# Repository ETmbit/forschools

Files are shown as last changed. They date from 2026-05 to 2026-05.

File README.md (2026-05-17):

ElecTricks


# Het ETmbit-project
Het ETmbit-project biedt een **complete leerlijn robotica** en maakt het lesgeven erin eenvoudig en toegankelijk. Het project is gericht op:
- bovenbouw basisonderwijs 
- onderbouw voortgezet onderwijs

ETmbit met **micro:bit + MakeCode**. Robotonderdelen worden **kant-en-klaar** aangeschaft of **3D-geprint**. Bij iedere module zit een **bouwgids** (inclusief bestellijsten en bestanden voor de 3D-printer), een **docentenhandleiding** en uiteraard het **lesmateriaal**. Van leerkrachten en docenten wordt **minimale voorkennis en voorbereiding** verwacht.

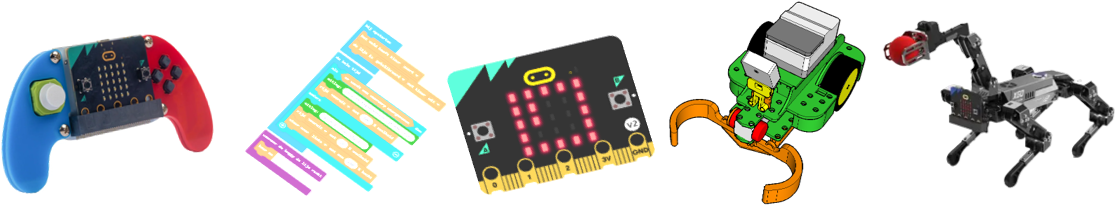
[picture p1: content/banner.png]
Banner


<br>

## :twisted_rightwards_arrows: Lesplan
ETmbit heeft **gedifferentieerd leren** als uitgangspunt. Leerlingen kiezen hun eigen route door het lesmateriaal op basis van interesse, niveau en leerstijl. Leerkrachten en docenten gebruiken een **volgsysteem** om hun ontwikkeling te begeleiden. Geen ingewikkelde sheets — alles werkt met voor zowel de leerlingen als de lesgevende **overzichtlijke routekaarten**.

:large_orange_diamond: [naar de routekaarten](NL/routekaarten/)

<br>

## :basket: Lesinhoud
Hier is **spelenderwijs leren** de boodschap. Het begint met enkele bekende spelletjes om te leren hoe MakeCode werkt: *kat-en-muis*, *snake*, *simon-says*. Het lesmateriaal biedt veel **challenges**. Via verschillende routes door het ETmbit-materiaal ontwikkelen leerlingen uiteindelijk dezelfde vaardigheden. Voor elk wat wils:

:soccer: sport, :musical_note: muziek, :cartwheeling: dans, :video_game: games, :seedling: natuur, :baby: verzorging, :nut_and_bolt: techniek, :clapper: beeld, enz.

:large_orange_diamond: [naar de lesmodules](NL/modules/)

<br><br>

## :movie_camera: En ...
Waarom *ElecTricks*? De naam komt van een tv-serie uit mijn jeugd:
<br><br>

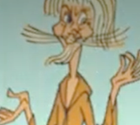
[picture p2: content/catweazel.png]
Catweazel


**Catweazel**. De in het heden belande middeleeuwse magiër, die de wonderlijke mogelijkheden van elektriciteit *Elec-Trickery* noemde.

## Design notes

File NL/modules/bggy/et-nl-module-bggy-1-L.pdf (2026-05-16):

45

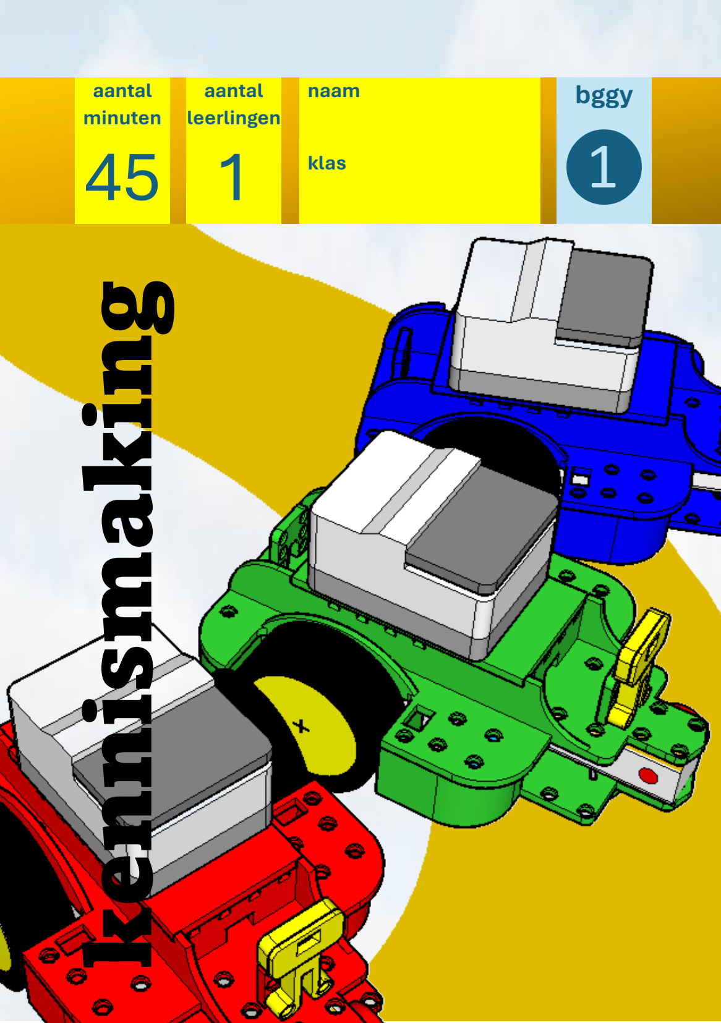
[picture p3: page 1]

bggy ❶

aantal
minuten

aantal
leerlingen 1

naam

klas

# kennismaking

### Nodig:

- De buggy
- Het veld voor de lijnvolger
- Een voorwerp van ongeveer 20 cm hoog en breed
- MakeCode
url = https://makecode.microbit.org
- Uitbreiding ETmbit/etbuggy
url = https://github.com/ETmbit/etbuggy

### Het blokkenmenu:

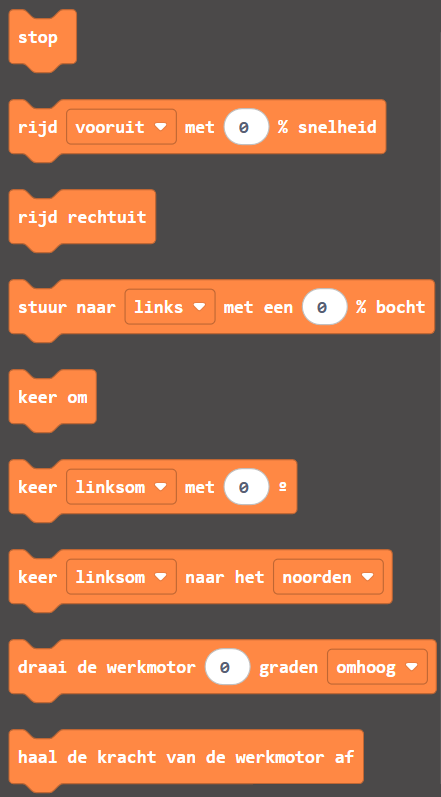
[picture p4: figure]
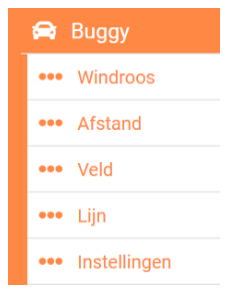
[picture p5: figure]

Voordat je begint moet je met de instellingen de buggy klaar maken om te programmeren.

In het hoofdmenu
hiernaast vind je de
blokken om de buggy
te besturen.
Met de blokken van de
extra menu’s hieronder,
gebruik je de sensoren.

### De buggy:

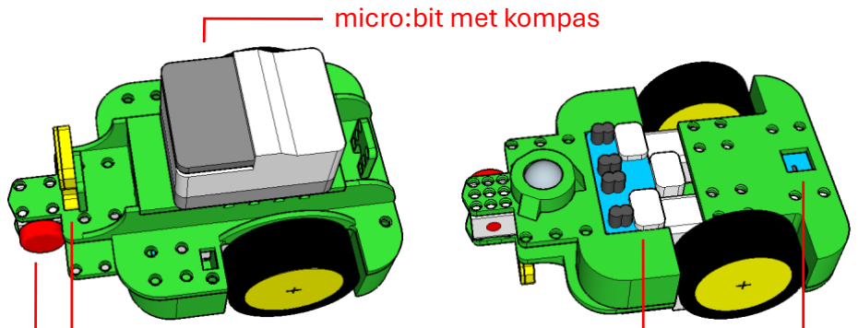
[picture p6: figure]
micro:bit met kompas

### Toelichting bij enkele codeblokken:

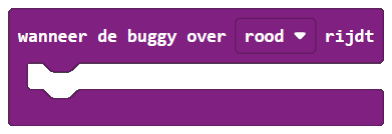
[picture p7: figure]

De kleur wordt door de veldsensor gemeten.
Een bocht van 0% gaat rechtuit. Bij een bocht van 100% draait de buggy om zijn as.
‘Omhoog’ betekent dat
de voorkant van de
motoras omhoog draait.
Normaal houdt de werkmotor iets opgetild.
werkmotor | afstandsensor | lijnsensor | veldsensor

### Begin met de instellingen:

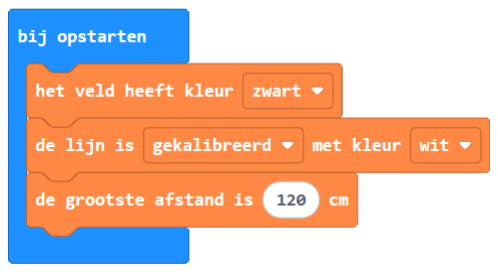
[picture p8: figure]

De belangrijkste instelling is die van de veldkleur. Als je die vergeet, zal de buggy niet rijden.
Het is het beste om de lijnsensor van de buggy op het veld met de lijn te kalibreren:

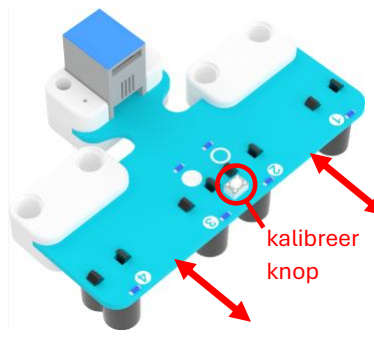
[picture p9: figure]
kalibreer knop

Je moet ook laten weten tot hoever de buggy afstanden zal meten. Daarbinnen mag niemand staan.

1. Druk op de kalibreerknop.
2. Leds 1 t/m 4 gaan om de beurt aan.
3. Leds ○ en ● knipperen snel.
4. De verlichting onder gaat aan.
5. Beweeg de sensor 1 cm boven de grond vanaf het veld over de lijn heen en weer.
6. Doe dit tot het knipperen stop.

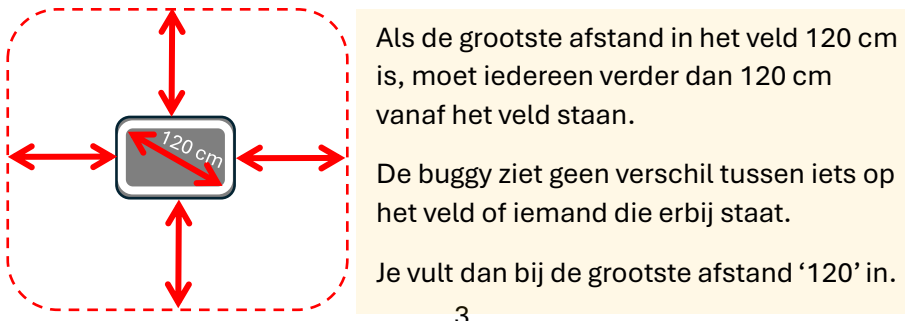
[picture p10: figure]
is, moet iedereen verder dan 120 cm vanaf het veld staan.; het veld of iemand die erbij staat.

Als de grootste afstand in het veld 120 cm

De buggy ziet geen verschil tussen iets op

Je vult dan bij de grootste afstand ‘120’ in.

### Probeer de volgende programma’s:

Gebruik nu het veld voor de lijnvolger. Dit heeft een witte lijn op een zwart veld.
Maak één voor één de volgende programma’s en kijk wat er wel/niet gebeurt. Begin steeds midden in het veld.
- 1

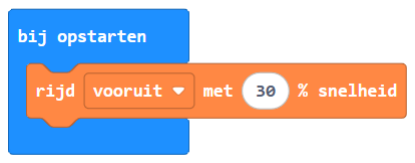
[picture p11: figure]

- 2

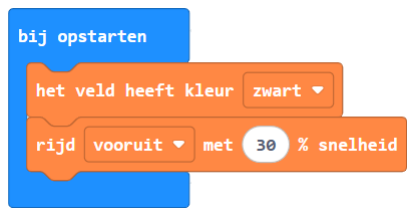
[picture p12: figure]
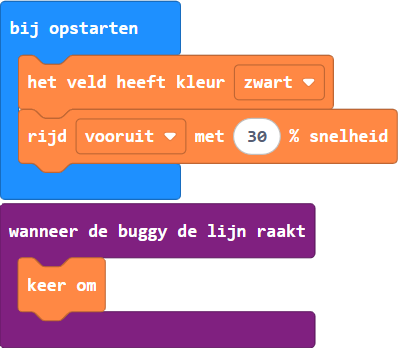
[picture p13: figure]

Let op: Vul de echte kleur van het veld in.

- 3

Laat de buggy naar een
voorwerp rijden.
- 4

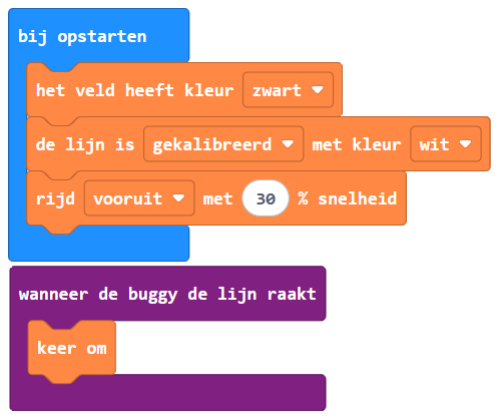
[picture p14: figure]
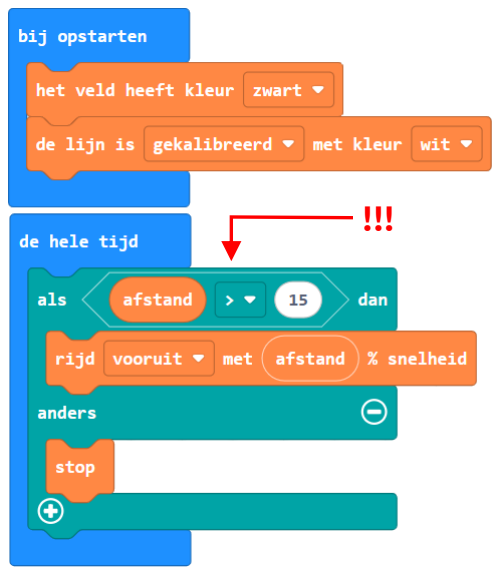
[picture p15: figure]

Let op: Vul de echte kleur van de lijn in.

- 5

### Verwerking:

Beantwoord de volgende vragen:
Wat gebeurt er als je geen veldkleur instelt?
- De buggy doet helemaal niets.
- De buggy begint, maar stopt meteen.
- De buggy doet het gewoon.
Waarom denk je dat dit zo is?
- Dan weet je dat de buggy iets doet.
- Anders kan de buggy van tafel rijden.
- Beiden zijn waar.
Hoe reageert de buggy op de lijn?
- Dat programmeer je met
- De buggy stopt op de lijn.
- De buggy keert om bij de lijn.
Wat moet je doen om | te laten werken?
- Het is genoeg om de buggy aan te zetten.
- Altijd als de buggy bij de lijn komt.
- Je moet niet vergeten de lijn in te stellen.
Bij programma 5 gaat de buggy steeds langzamer rijden. Welk blok doet dat?
○
○
○

### Zelf doen:

Denk om wat je tot nu toe hebt geleerd.
Je kunt ook de volgende blokken gebruiken:

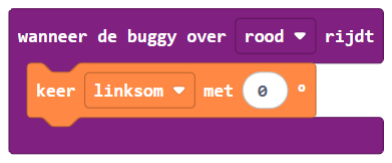
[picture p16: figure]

- 1

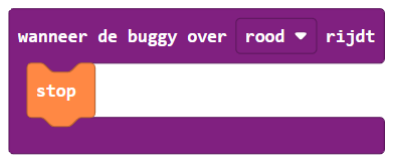
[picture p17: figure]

Maak een programma waarmee de buggy op een gekleurd vak stopt.

- 2
Maak een programma waarmee de buggy tussen de vier gekleurde vakken een rondje rijdt.

Tip.
Zo werkt het met graden:
0⁰ | 90⁰ | 180⁰ | 270⁰ | 360⁰

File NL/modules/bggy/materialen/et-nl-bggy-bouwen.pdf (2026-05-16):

# ETBUGGY

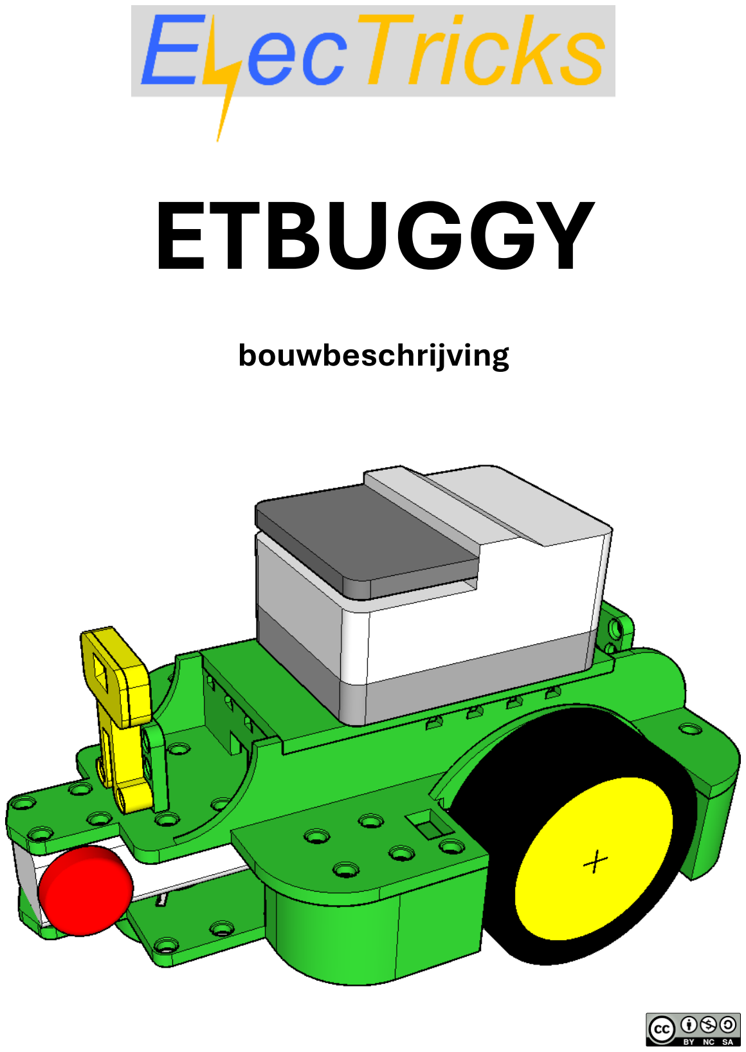
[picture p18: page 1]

bouwbeschrijving

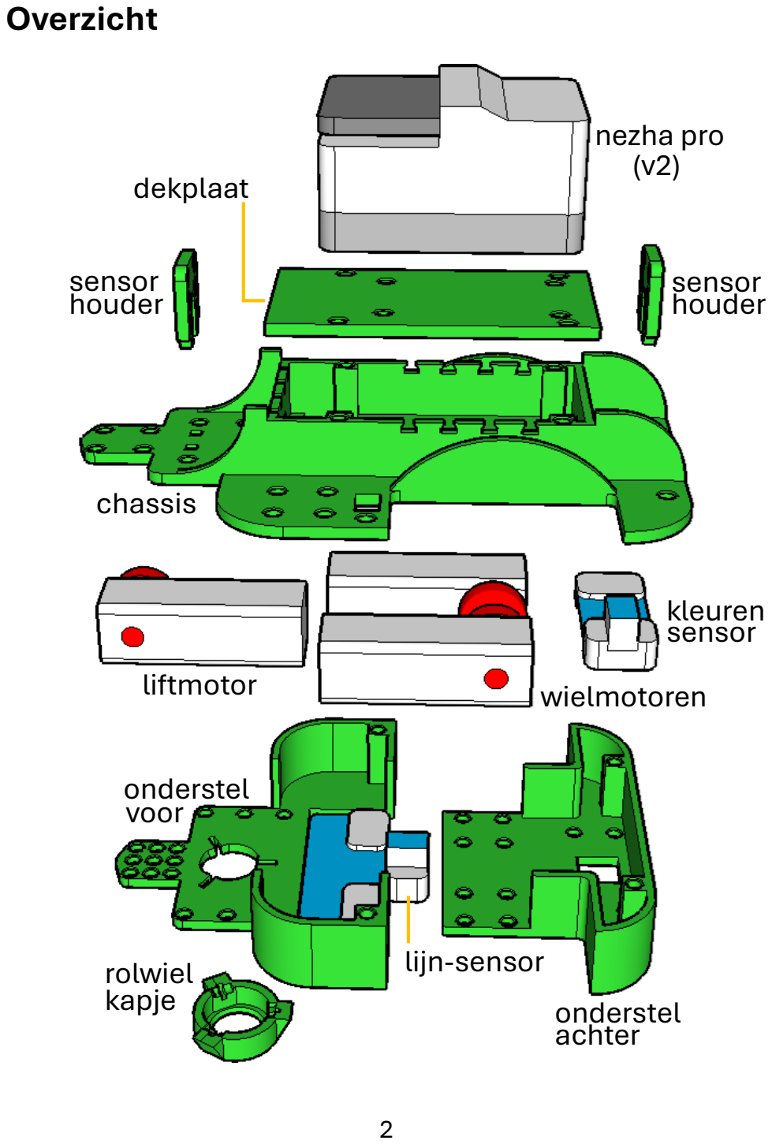
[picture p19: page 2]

Overzicht

chassis

dekplaat

nezha pro

sensor
houder

wielmotoren liftmotor

sensor
houder

onderstel
achter

onderstel
voor

lijn-sensor

(v2)

kleuren
sensor

rolwiel
kapje

Maken en kopen

De volgende onderdelen worden met een 3D-printer gemaakt. De stl-bestanden zijn te vinden in: https://github.com/etmbit/printables
chassis: | et-nl-bggy-chassis.stl
dekplaat: | et-nl-bggy-dekplaat.stl
onderstel voor: | et-nl-bggy-voorkant.stl
onderstel achter: | et-nl-bggy-achterkant.stl
sensorhouder voor: | et-nl-bggy-sensor-voor.stl
sensorhouder achter: et-nl-bggy-sensor-achter.stl
rolwielkapje: | et-nl-bggy-caster.stl
asje voor kogellager: et-nl-bggy-caster-asje.stl
lidar-afstandsensor: et-nl-bggy-lidar.stl | *)
wielasje TT/LEGO: | et-nl-bggy-tt2lego.stl
motoras met dop: | et-nl-bggy-motor-as.stl

*) Dit is de behuizing voor de VL53L1X-lidar (zie verderop).

De onderdelen voor het rolwiel (een kogel met drie lagers) zijn verkrijgbaar bij www.neita.nl/webshop:
Kogel: Home > Webshop > Lagers > Kogels
> Kogels 22mm DIN 5401 GD-20 Lagers: Home > Webshop > Lagers > Miniatuurlagers > PRC Miniatuur kogellager 1R (5x8x2,5)

De wielen en een lidar-afstandsensor zijn te bestellen bij www.tinytronics.nl/nl:
Wielen: | Home > Mechanica en Actuatoren > Onderdelen > Wielen > Reservewiel - Auto Kit - Zelfbouw

Afstandsensor: Home > Sensoren > Afstand
| > VL53L1X Time-of-Flight ToF
Voor de lidar-afstandsensor is het nodig om een aan één uiteinde gestripte PlanetX RJ11-kabel aan de VL53L1Xsensor te solderen. De behuizing kan met een 3D-printer worden gemaakt (gebruik het eerder genoemde bestand buggy-lidar.stl).
Aansluitschema:

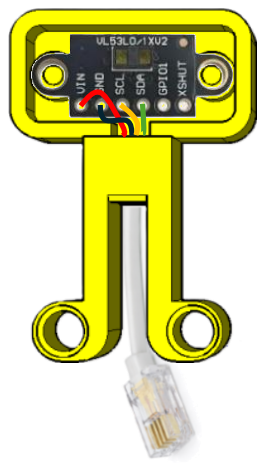
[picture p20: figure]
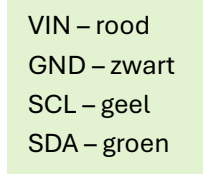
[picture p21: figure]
VIN – rood GND – zwart SCL – geel SDA – groen

In plaats van deze lidar, kan ook een ultrasone afstandsensor worden gebruik, zoals het kant-en-klare model uit de PlanetX-serie (zie hierna).

lijmen

De electronische onderdelen komen uit de PlanetX-serie van Elecfreaks en kunnen afzonderlijk worden besteld bij webshop.ictleskisten.nl/product-categorie/elecfreaks:
nezha pro: | Nezha PRO breakout board [EF05070]
motoren: | Smart Brick Motor [EF05071]
lijnsensor: | 4 Channel Tracking Sensor [EF05053]
kleurensensor: Colour Sensor [EF05006] afstandsensor: Ultrasonic Sensor [EF05007] *)
snoeren: | RJ11 4P4C 200 mm Kabel [EF05049]

*) Eventueel ter vervanging van de lidar-sensor (zie hiervoor).

Om de verschillende onderdelen aan elkaar te
bevestigen, zijn 36 pinnen | en 2 pinnen | nodig. Deze
zijn te verkrijgen bij www.steentjeswereld.nl:
pin | : | zoek LEGO-technic onderdeel 32002
pin | : | zoek LEGO-technic onderdeel 2780

De behuizing van de lidar-afstandsensor en het rolwielkapje moeten worden gelijmd. Gebruik bijvoorbeeld BISON HARD PLASTIC LIJM. Deze is te verkrijgen bij een doe-het-zelver of bouwmarkt.

Bouwen

LET OP:
De afbeeldingen geven alleen de constructie weer en niet de bouwvolgorde. Bijvoorbeeld wordt de dekplaat pas geplaatst nadat de bedrading is voltooid.
Verder worden permanente verbindingen met rode lijnen en losneembare met blauwe lijnen afgebeeld. Tenslotte: Let er bij de -pinnen goed op waar het korte en waar het lange eind hoort te zitten.

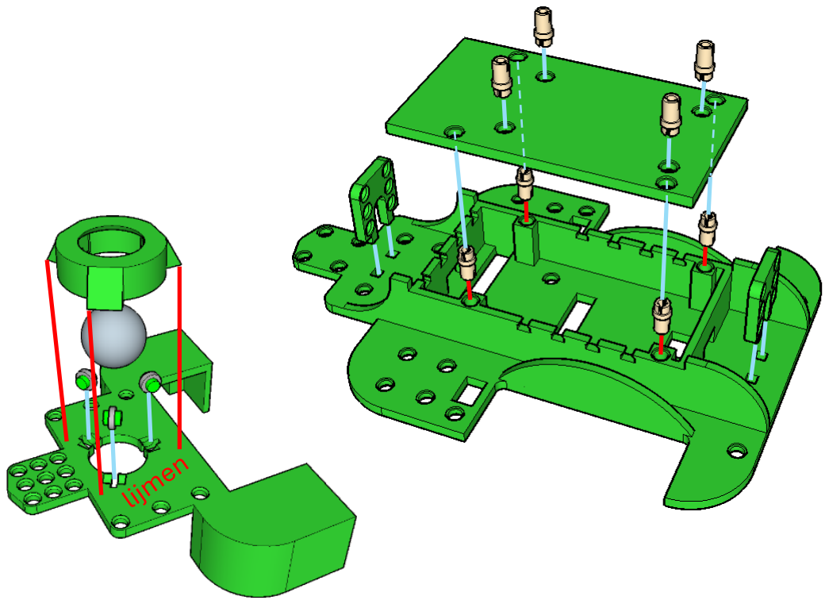
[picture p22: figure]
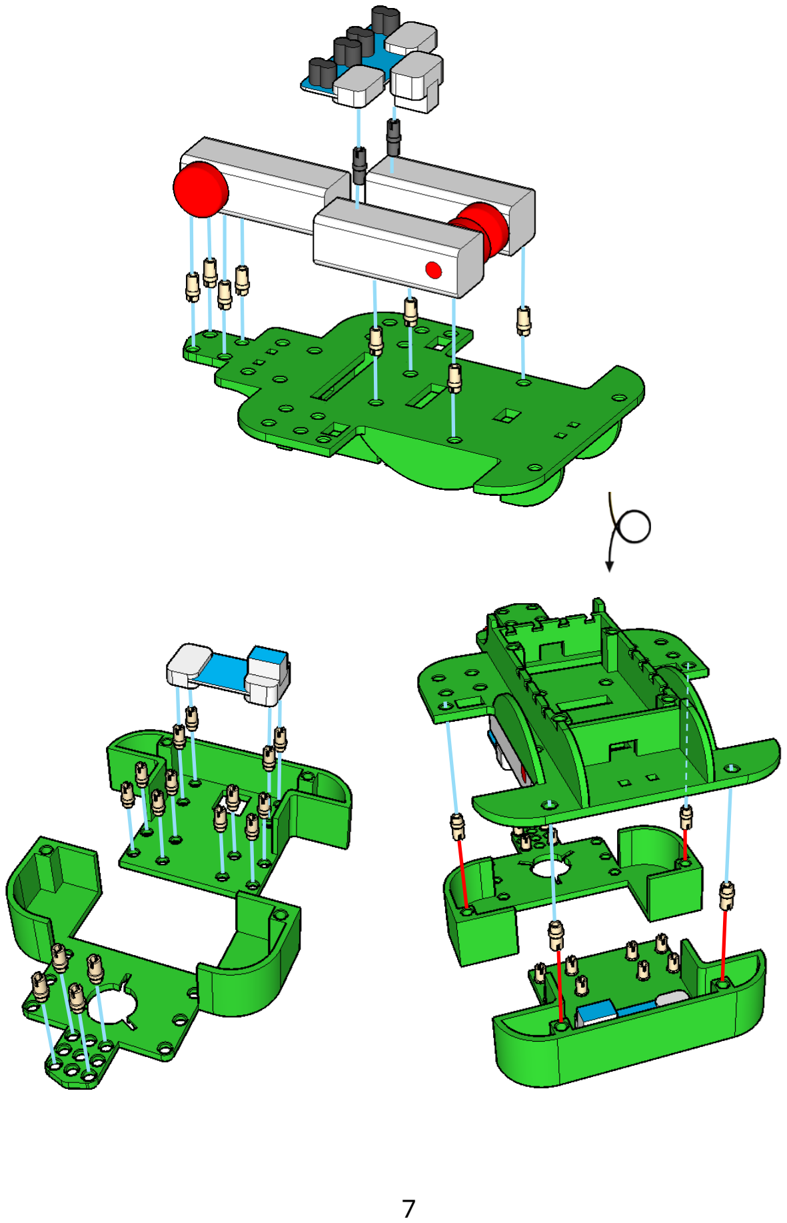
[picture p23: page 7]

Sluit de snoeren aan voordat het chassis en het onderstel op elkaar worden gemonteerd. Om een snoeren-spagetti te voorkomen, worden de snoeren als volgt aangesloten: ❶ Sluit de snoeren op de motoren en sensoren aan.
❷ Trek de snoeren zover mogelijk door de uitsparingen in het chassis.
❸ Wikkel overtollig snoer in het opslagvak.
❹ Duw de uiteindes van de snoeren vast in de daarvoor aangebrachte sleuven van het chassis.
❺ Sluit het geheel af met de dekplaat.
❻ Sluit de uiteindes van de snoeren op de nezha-pro aan.

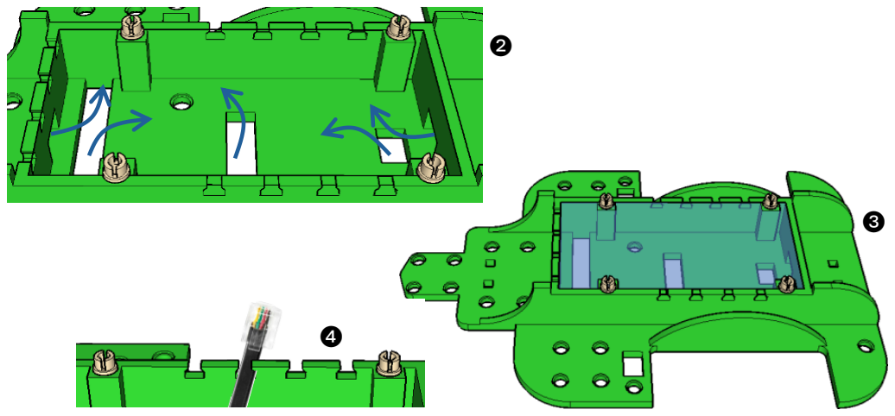
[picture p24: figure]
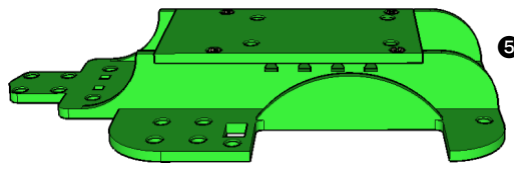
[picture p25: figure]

❺

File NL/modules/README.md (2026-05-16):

ElecTricks

# ETmbit lesmodules

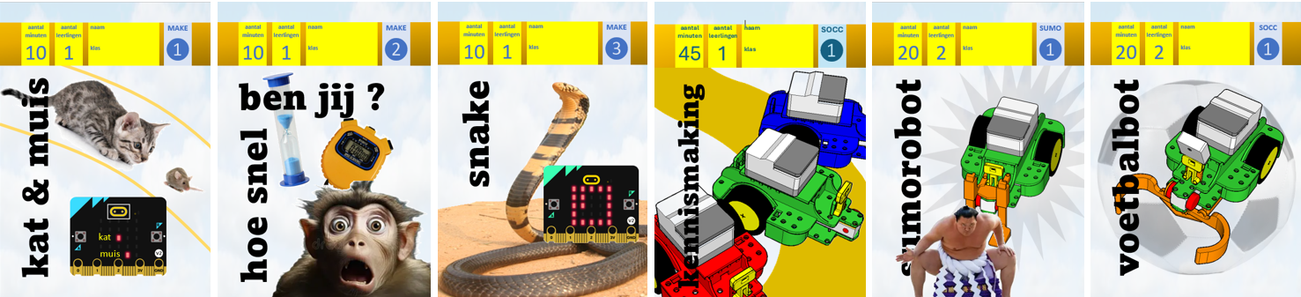
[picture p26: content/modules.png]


In de rechter bovenhoek bevindt zich de modulenaam en het volgnummer van de opdracht. Deze komen overeen met die op de routekaart.

## Document-versies
De opdrachten zijn op A5-formaat vormgegeven. Als boekje nemen ze weinig ruimte in. Er staat immers ook een robot naast de computer.

De bladzijden van de *...-B.pdf*-versies zijn als boekje gerangschikt. Gebruik deze versies om leerlingboekjes te printen.
**Printereigenschappen**: dubbelzijdig afdrukken via de korte zijde.<br>
Nieten kan met een langarm-nietmachine, bijvoorbeeld https://www.manutan.nl/nl/mnl/langarm-nietmachine-rapid-hd12.

De versies eindigend op *...-L.pdf* bevatten losbladig gerangschikte pagina’s. Deze versies zijn vooral geschikt voor presentaties of voor weergave in github.

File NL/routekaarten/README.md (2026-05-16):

ElecTricks

# ETmbit routekaarten

ElecTricks

De routekaarten geven per leerling een overzicht van de persoonlijke leerroute binnen ETmbit.

## Zo werkt een routekaart

Een routekaart laat per leerling in één oogopslag zien:

* welke modules op welk moment gedaan zijn,
* welke route gevolgd is,
* en welke vervolgstappen mogelijk zijn.

<br>

In het voorbeeld van Caroline betekent dat:

* Caroline startte vorig jaar in **M1D**.
* Ze zit nu in **M2C**.
* Vanuit de basisroute koos ze de route **SUMO** (sumorobot).
* Daarna volgde ze de **soccer-routekaart**.
* Als ze later nog **BGGY-3** wil doen, moet ze eerst ook **BGGY-1** of **BGGY-2** afronden.

## In de praktijk

1. Elke leerling begint op de oranje startpijl van **et-nl-routekaart-basis.pdf**.
2. Uit parallelle modules — samen weergegeven in een lichtblauw vak — kunnen leerlingen zelf kiezen.
3. Afhankelijk van de keuzes en behaalde modules worden extra routekaarten toegevoegd.
4. Die komen in de klassemap vóór de basisroutekaart van de leerling.
5. Zo ontstaat voor iedere leerling een persoonlijk leerpad dat zichtbaar blijft over meerdere jaren.

In de praktijk wordt een klassemap vaak georganiseerd met per leerling een eigen mapje of tabblad.

## Beoordeling van de voortgang

Bij iedere module hoort een **opdrachtboekje**. Aan de hand daarvan vindt de beoordeling plaats. Het afronden van een opdrachtboekje is vergelijkbaar met het inleveren van een toets: hiermee laat de leerling zien of de leerdoelen van de module behaald zijn.

Bij onvoldoende verwerking kan ervoor worden gekozen om een leerling eerst een parallelle module — zoals bij MAKE-1 tot en met MAKE-3 — te laten volgen. Zo krijgt de leerling gelegenheid om de benodigde vaardigheden en leerdoelen alsnog voldoende te ontwikkelen.

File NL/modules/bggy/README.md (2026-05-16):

ElecTricks

# ETmbit Buggy

## Veilig in gebruik

Buggy Init

Module **BGGY-1** laat leerlingen kennismaken met het veilig gebruik van de buggy. De bijbehorende MakeCode-uitbreiding is zo ontworpen dat de buggy niet wil rijden zolang de veldkleur niet is ingesteld. Zodra de veldkleur is gekozen, stopt de buggy automatisch wanneer hij een andere kleur detecteert, tenzij voor die kleur expliciet een actie is geprogrammeerd.

Buggy Init

De lijn neemt daarbij een bijzondere plaats in. Ook voor de lijn moet een kleur worden ingesteld. De buggy kan vervolgens in twee verschillende modi werken:

Buggy Init

1. **De lijn als begrenzing van het veld**<br>
De lijn vormt de rand van het werkgebied. Zodra de buggy buiten het veld komt, stopt deze automatisch.

2. **De lijn volgen**<br>
De lijn wordt gebruikt als pad om te volgen. In deze modus blijft de buggy rijden zolang hij de lijn detecteert en stopt hij juist wanneer hij van de lijn af raakt.

:warning: **Blijf alert!** De ingebouwde veiligheidsmaatregelen bieden geen volledige garantie dat de buggy nooit over de lijn rijdt. De kans hierop hangt af van de breedte van de lijn en de snelheid van de buggy. Bij hoge snelheden of een smalle lijn kan de lijnsensor de lijn mogelijk niet op tijd detecteren.

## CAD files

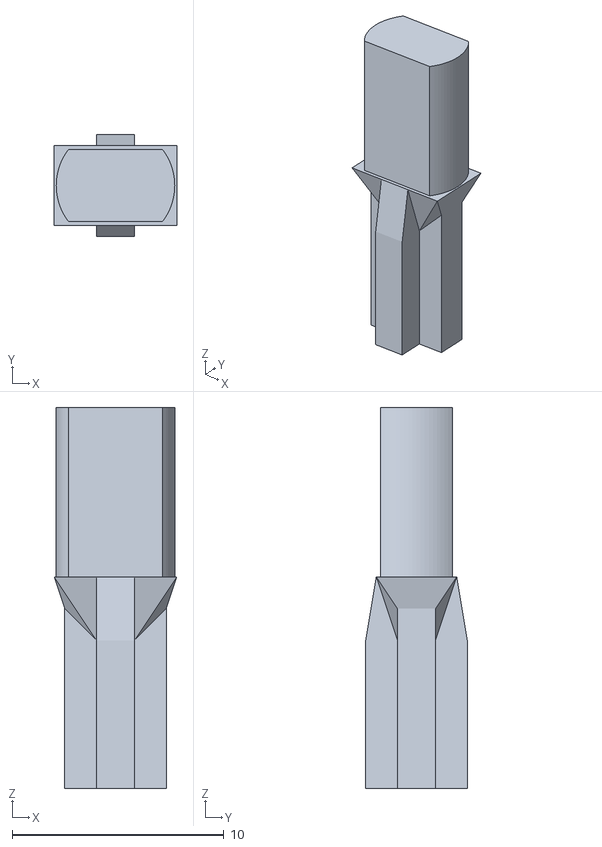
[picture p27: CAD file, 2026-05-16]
NL/modules/bggy/materialen/et-nl-bggy-tt2lego.stl
5.80 x 4.80 x 18.0

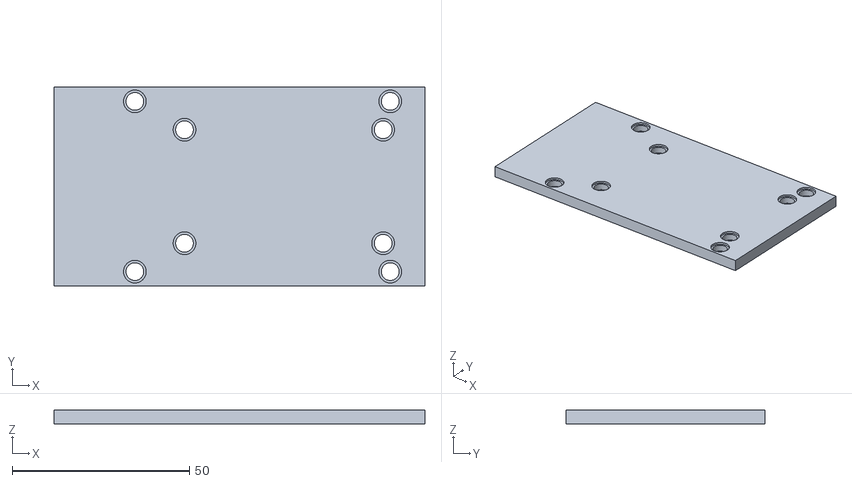
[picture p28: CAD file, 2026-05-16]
NL/modules/bggy/materialen/et-nl-bggy-dekplaat.stl
104.6 x 56.0 x 4.00

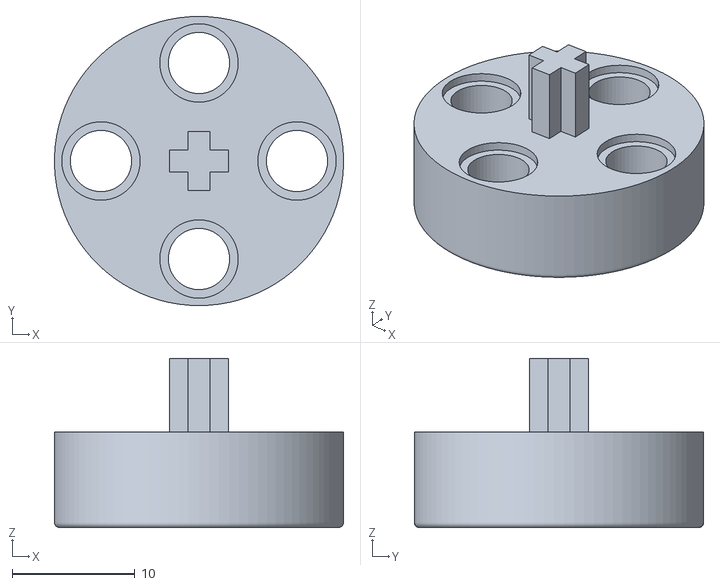
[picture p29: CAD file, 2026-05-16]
NL/modules/bggy/materialen/et-nl-bggy-motor-as.stl
23.6 x 23.6 x 13.8

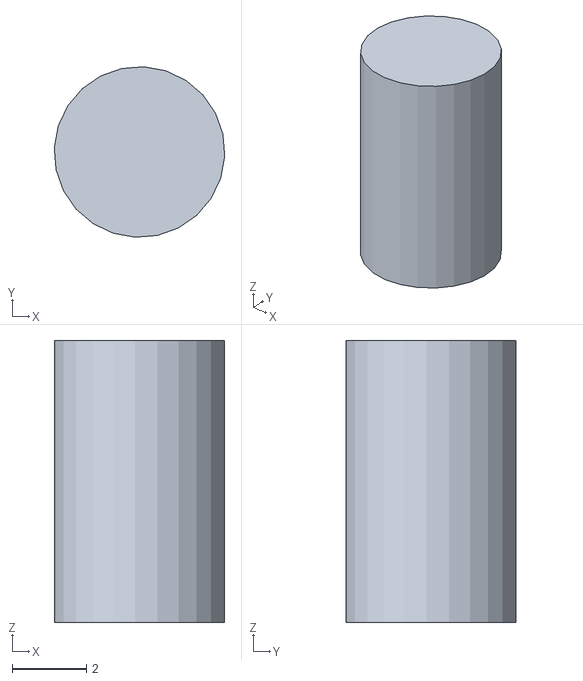
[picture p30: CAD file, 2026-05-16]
NL/modules/bggy/materialen/et-nl-bggy-caster-asje.stl
4.59 x 4.59 x 7.60

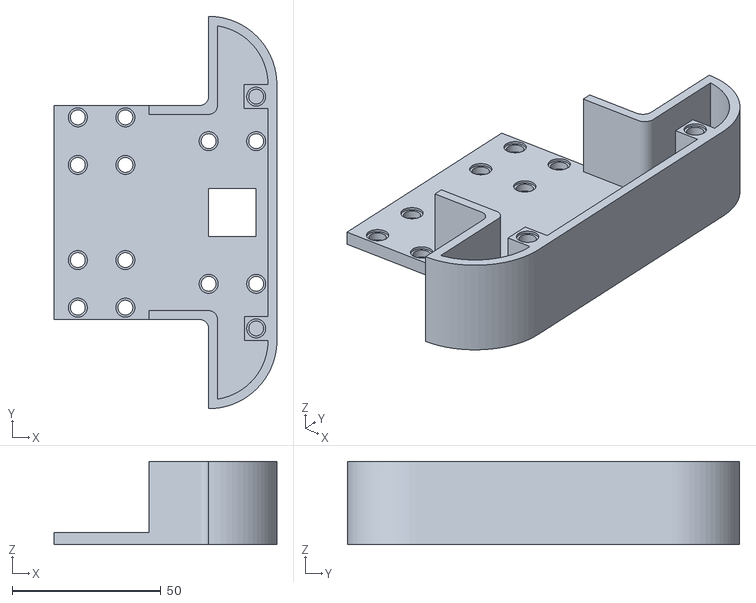
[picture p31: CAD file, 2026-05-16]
NL/modules/bggy/materialen/et-nl-bggy-achterkant.stl
75.0 x 132.0 x 28.0

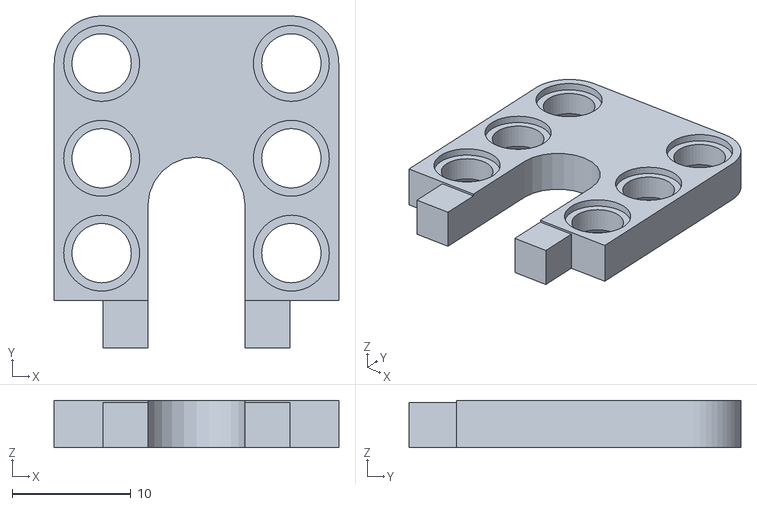
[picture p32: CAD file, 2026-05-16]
NL/modules/bggy/materialen/et-bggy-sensor-achter.stl
24.0 x 28.0 x 4.00

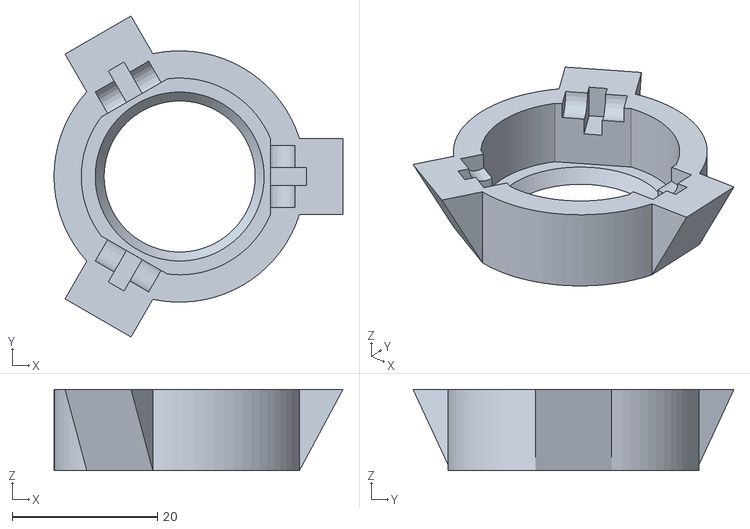
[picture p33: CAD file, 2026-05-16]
NL/modules/bggy/materialen/et-nl-bggy-caster.stl
39.8 x 44.2 x 11.2

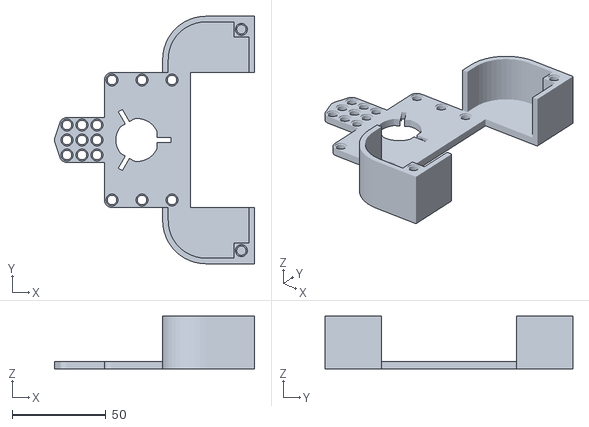
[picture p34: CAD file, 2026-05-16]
NL/modules/bggy/materialen/et-nl-bggy-voorkant.stl
106.7 x 132.0 x 28.0

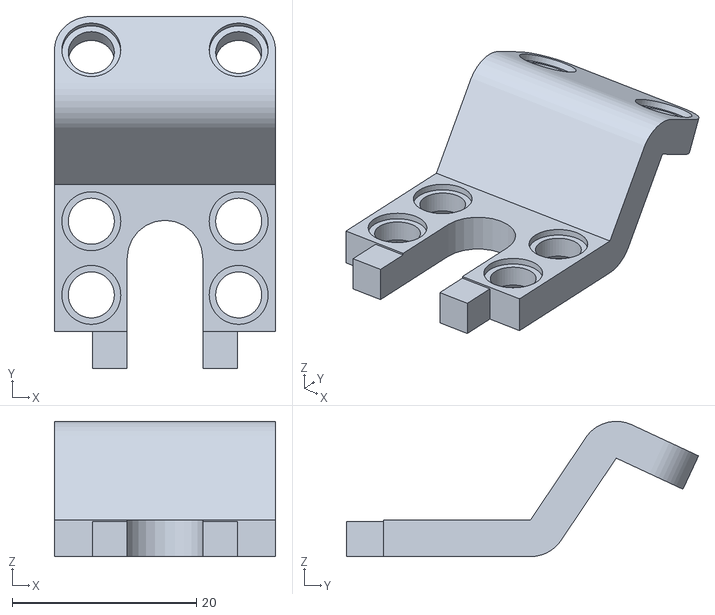
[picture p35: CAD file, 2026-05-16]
NL/modules/bggy/materialen/et-bggy-sensor-voor.stl
24.0 x 38.2 x 14.7

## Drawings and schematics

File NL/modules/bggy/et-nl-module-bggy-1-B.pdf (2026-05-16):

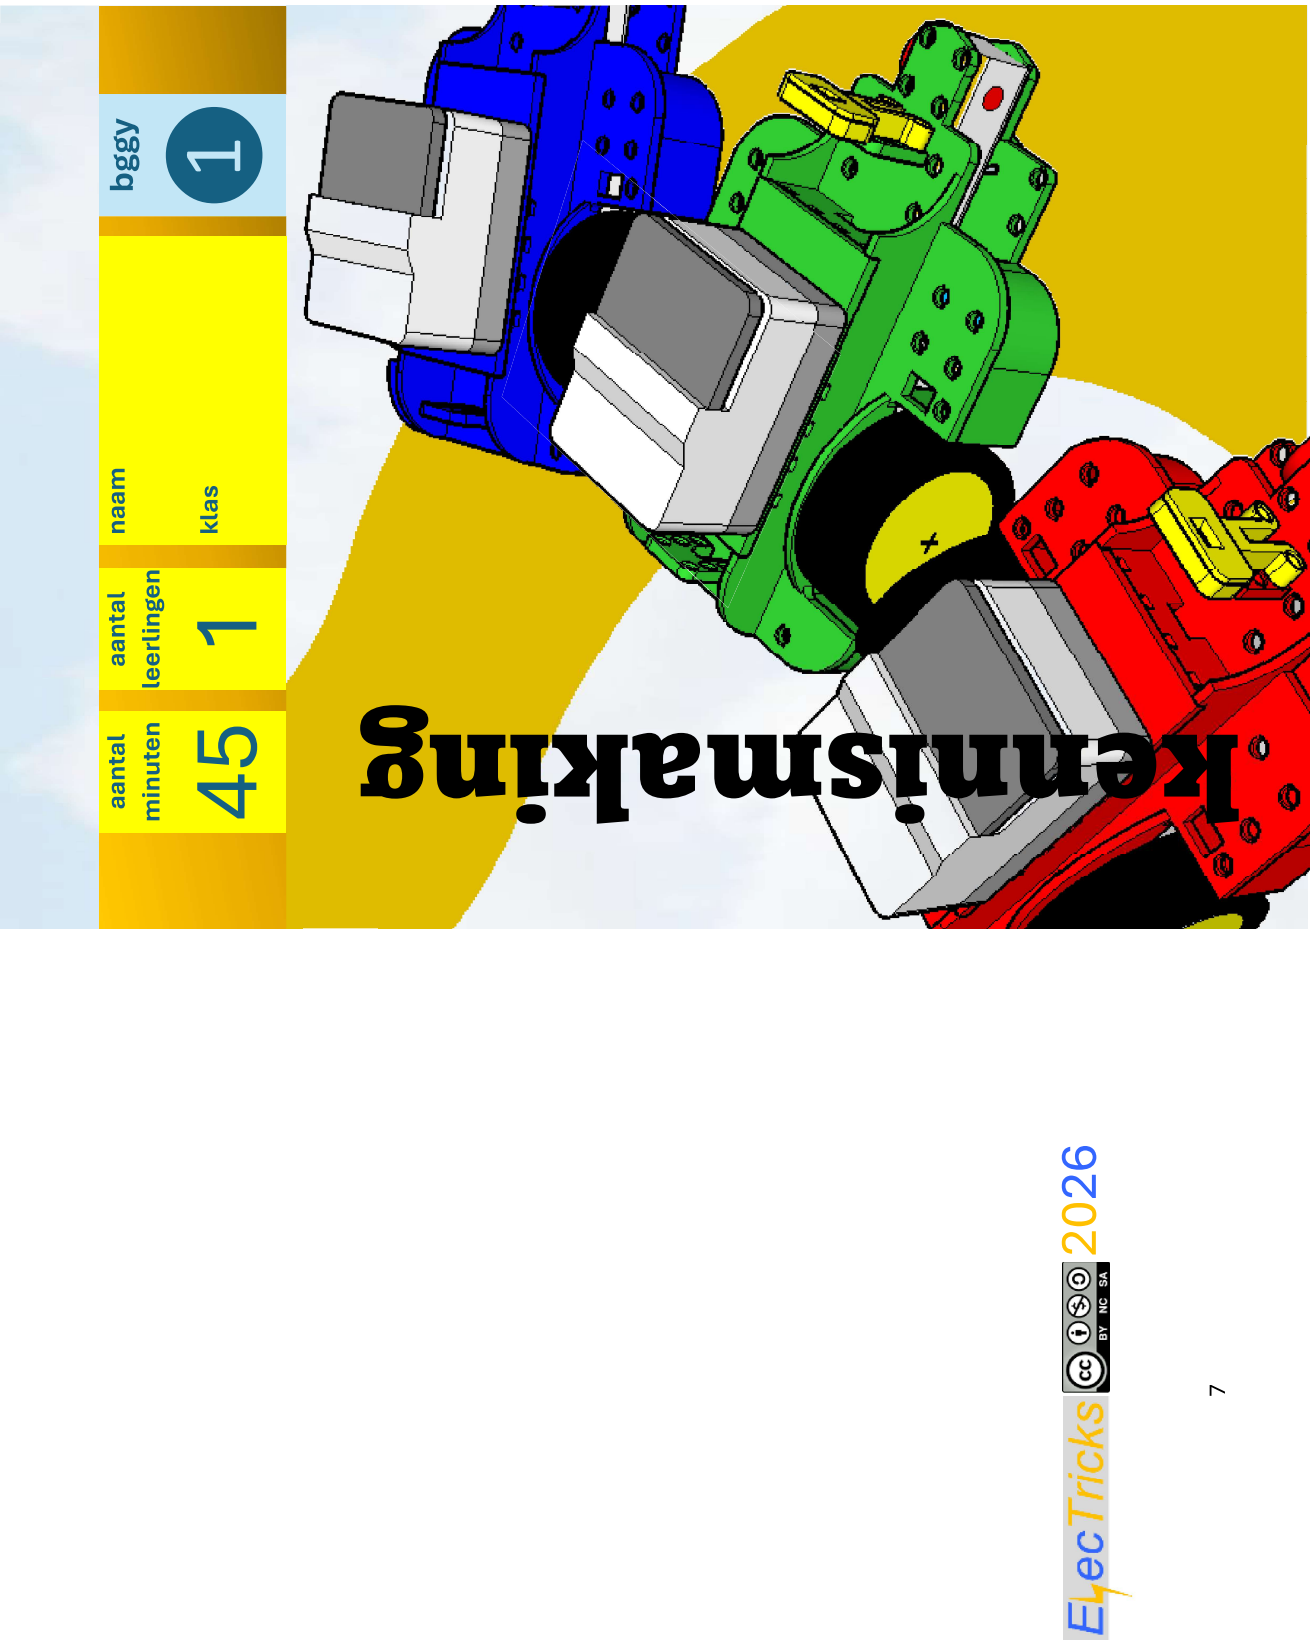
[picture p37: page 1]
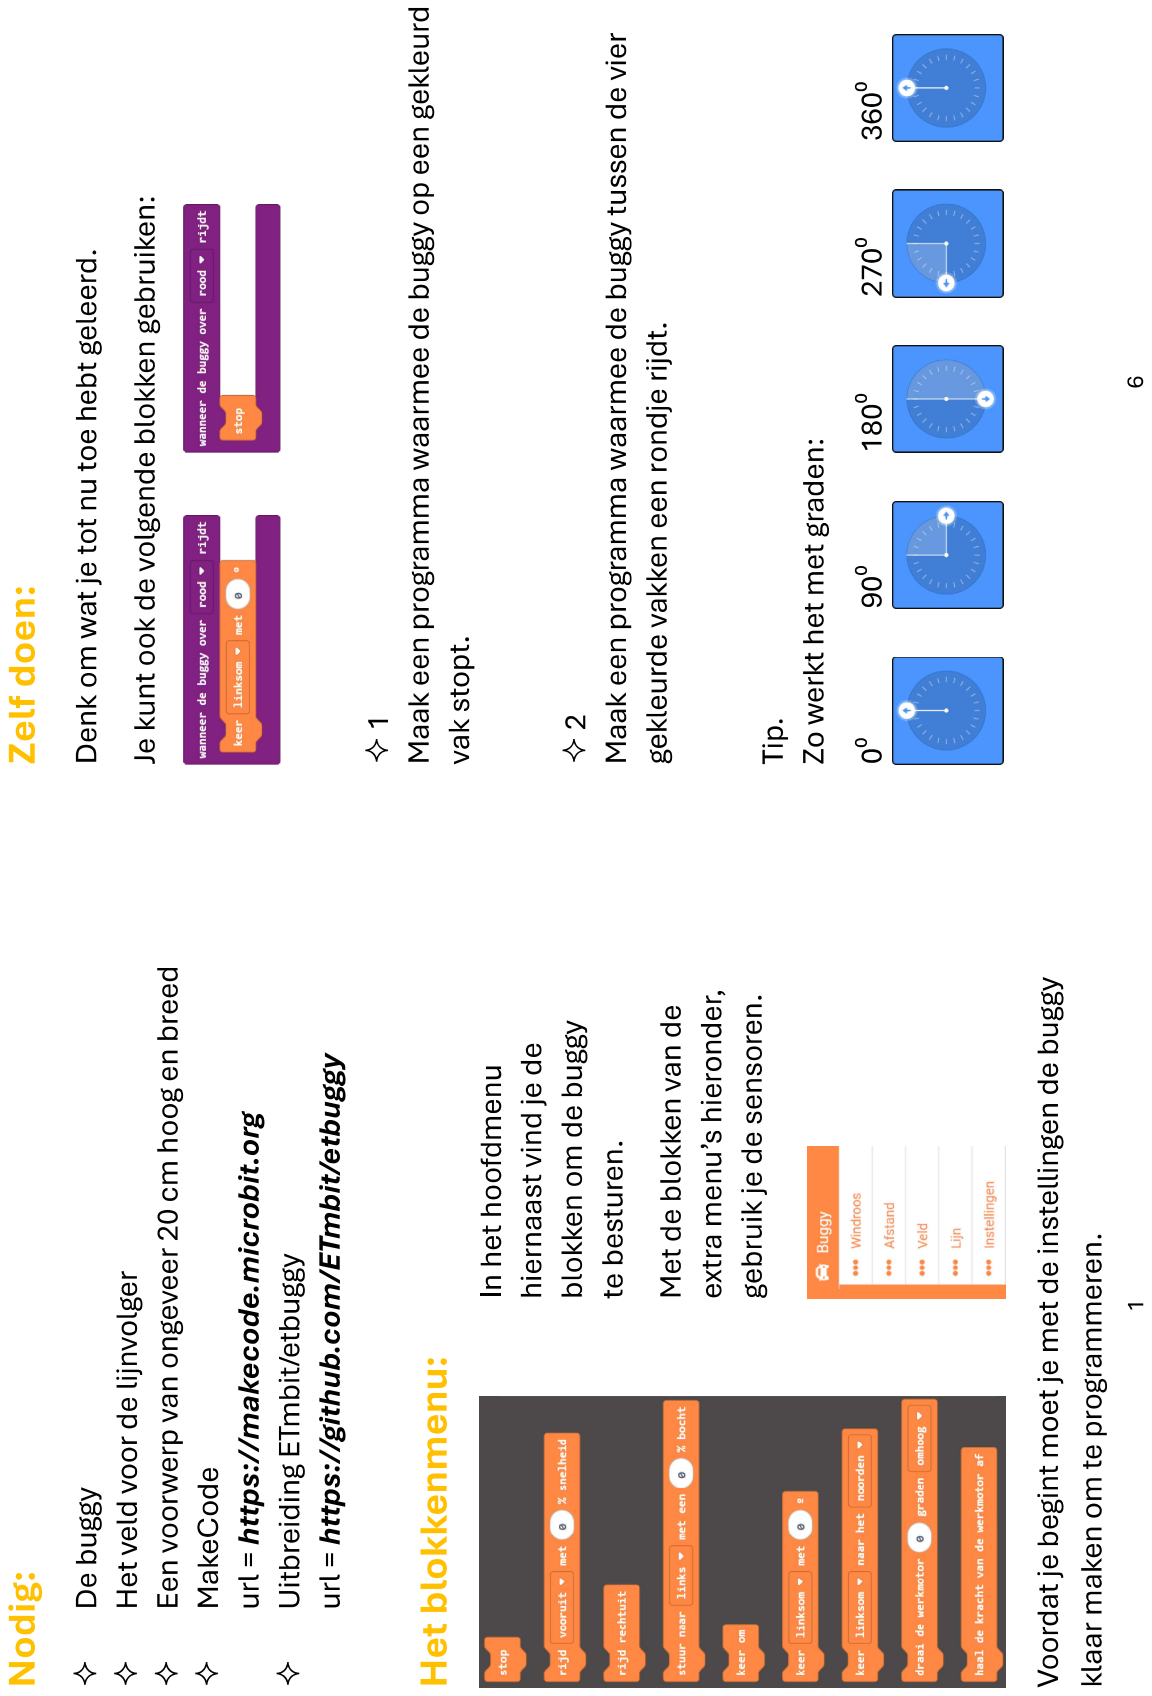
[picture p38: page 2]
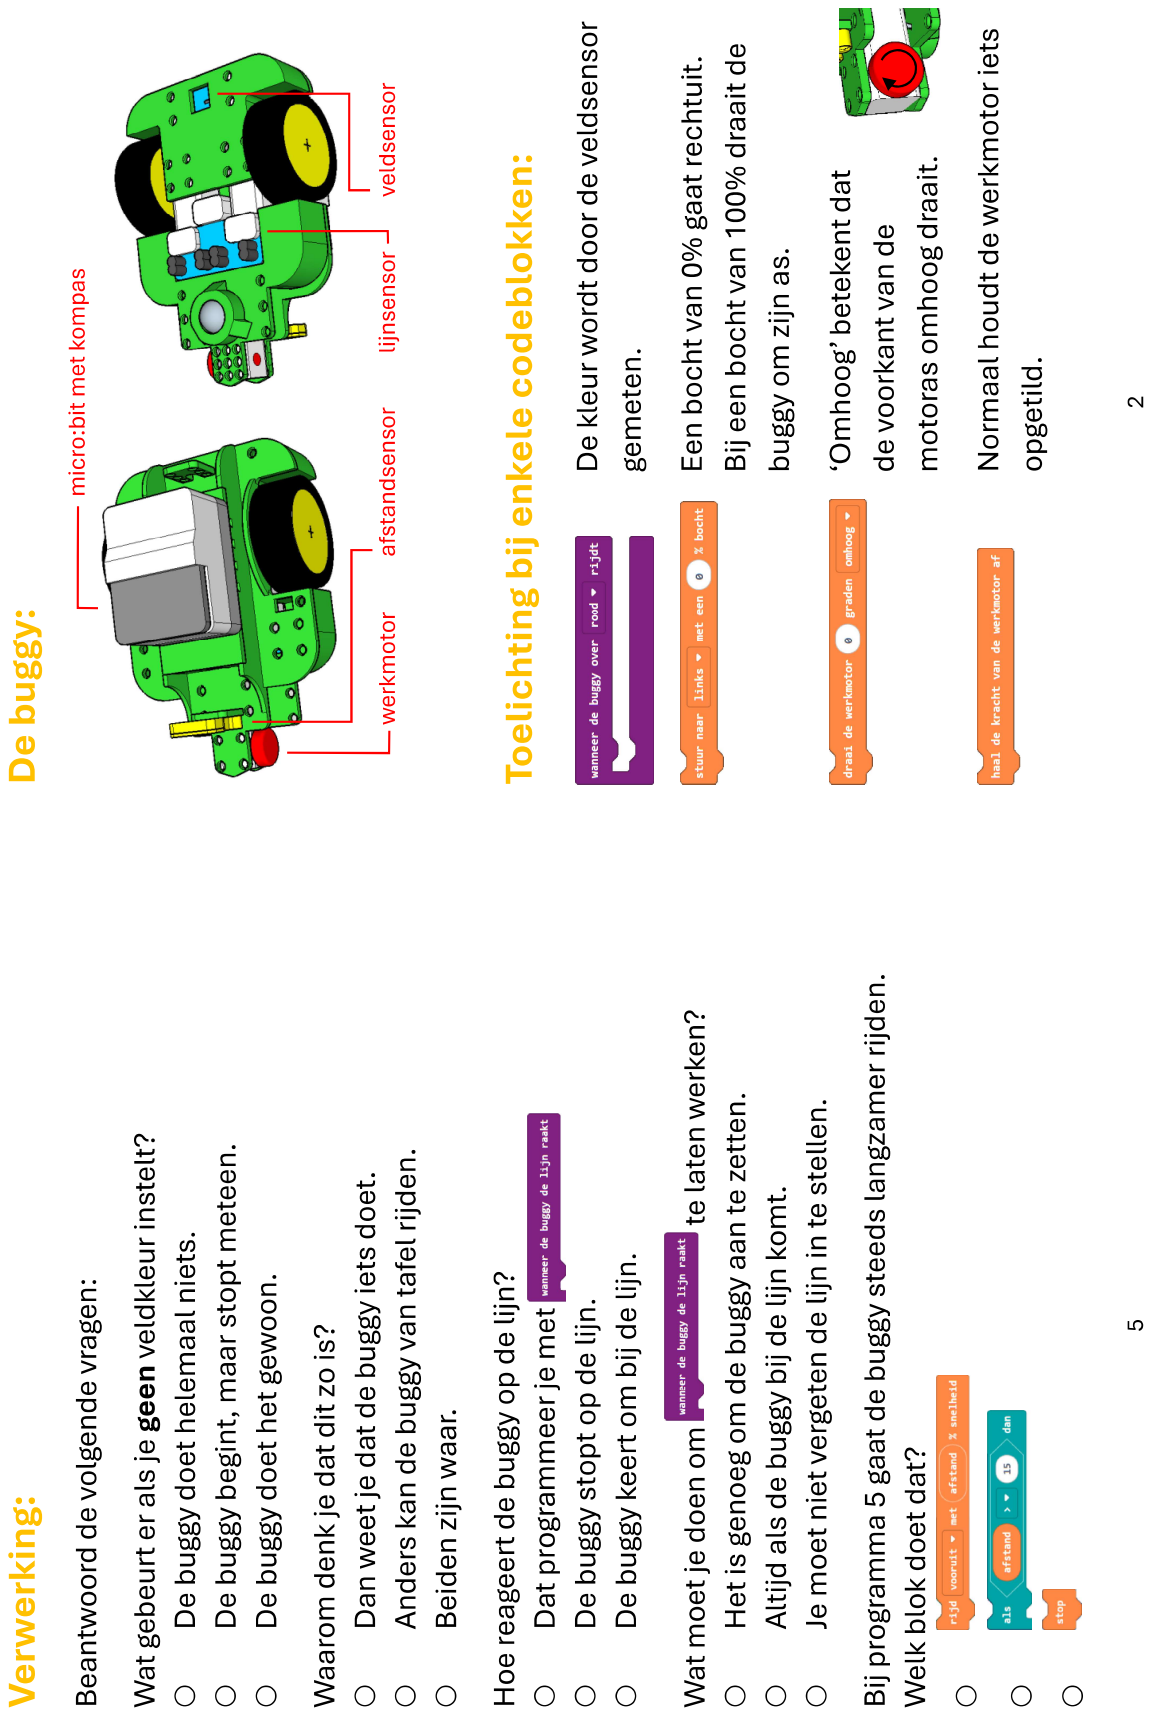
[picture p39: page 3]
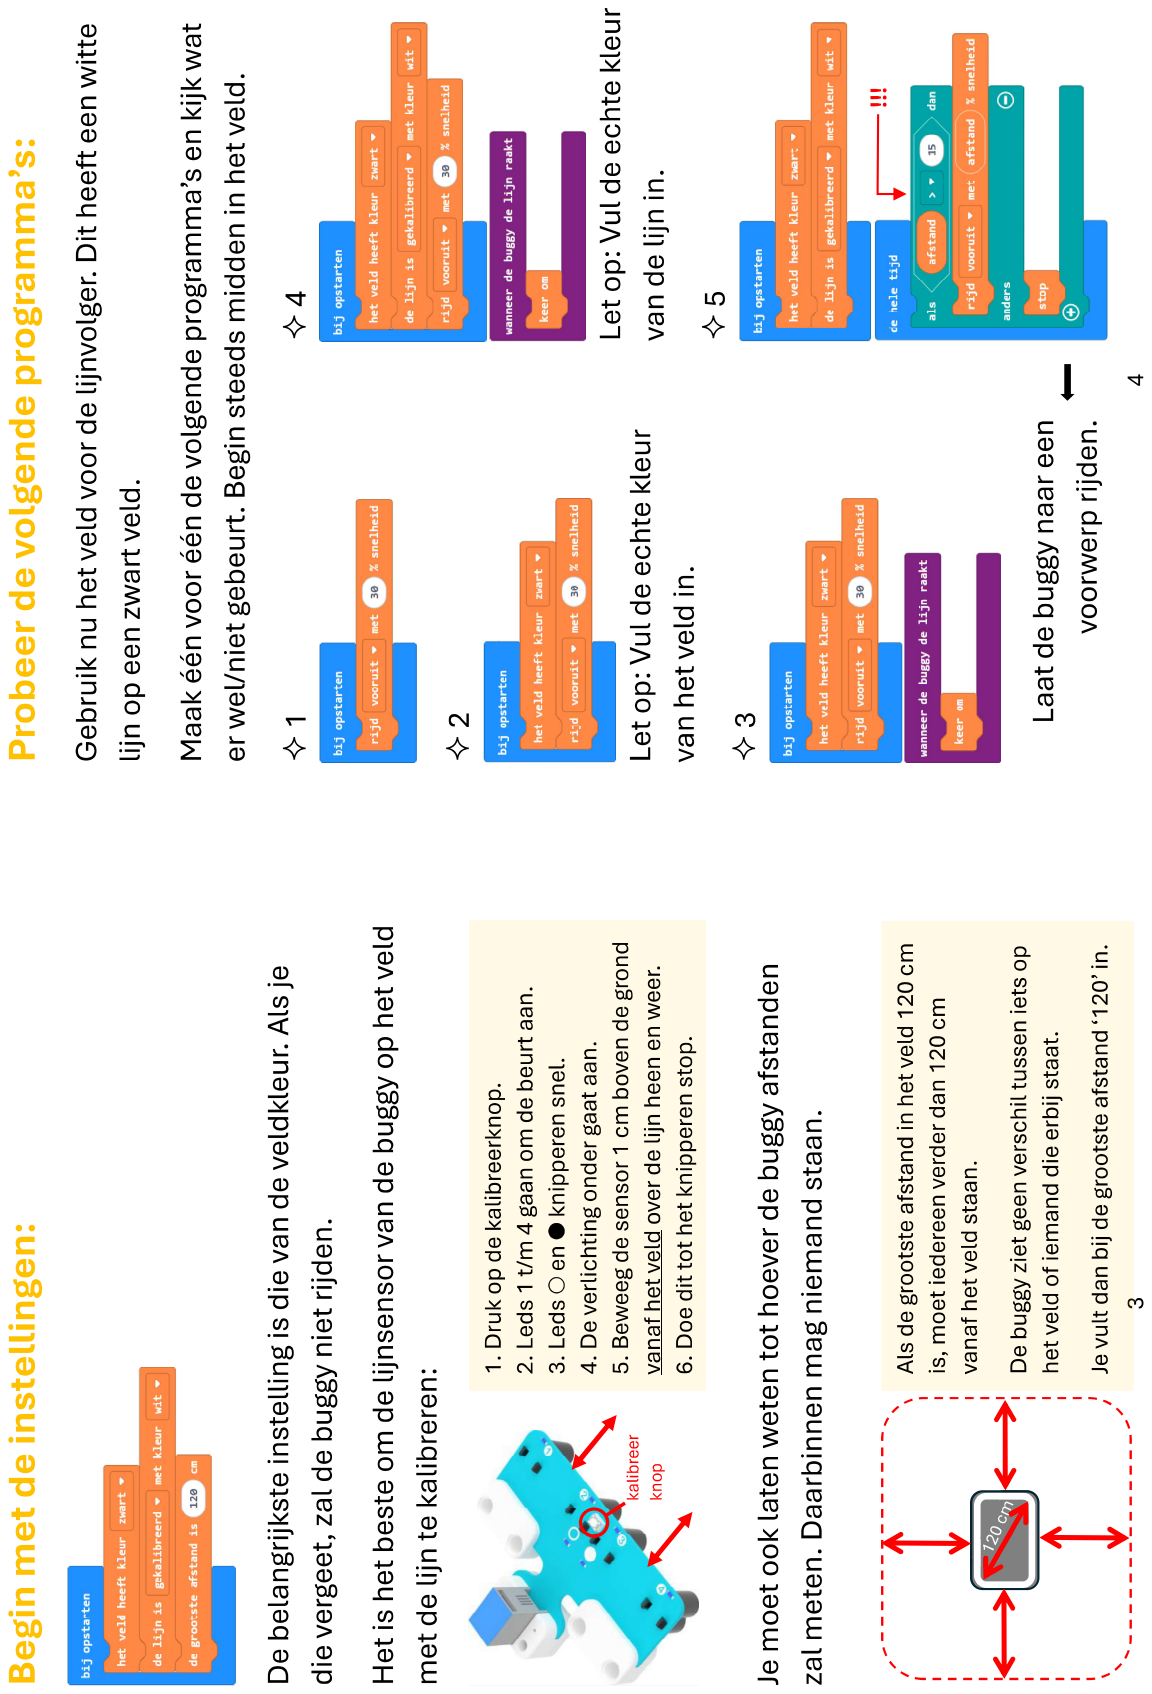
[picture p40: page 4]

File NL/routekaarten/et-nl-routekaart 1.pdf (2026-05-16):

## ROUTEKAART 1

van: | klas:

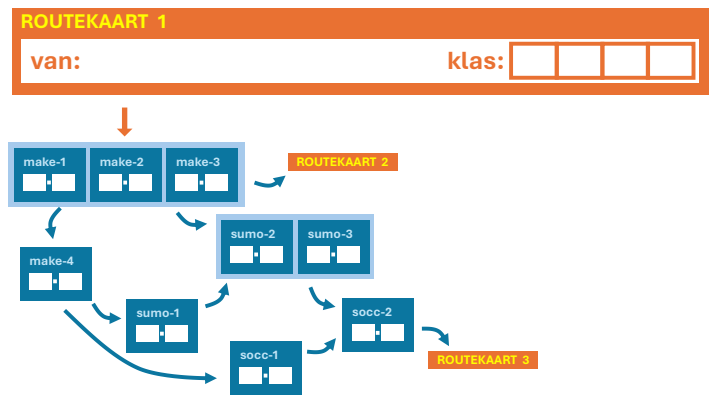
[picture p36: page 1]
make-1; make-2; make-3; make-4; sumo-2; sumo-3; sumo-1; socc-2; socc-1; ROUTEKAART 2; ROUTEKAART 3
